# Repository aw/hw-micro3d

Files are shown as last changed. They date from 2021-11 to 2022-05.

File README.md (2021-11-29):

# μ3D

### RatRig V-Core 3 EVA wiring over RJ45

A toolboard that mounts on a 3D printer hotend assembly to enable wiring over RJ45.

PCB top view

| | | |
| :----: | :----: | :----: |
|  | OSHW_mark_JP000011 (https://certification.oshwa.org/jp000011.html) | Hackaday Logo (https://hackaday.io/project/180918-3d-ratrig-v-core-3-eva-wiring-over-rj45) |
| [Buy on Tindie](https://www.tindie.com/products/24538/) | [OSHW Certification](https://certification.oshwa.org/jp000011.html) | [Hackaday.io Project](https://hackaday.io/project/180918-3d-ratrig-v-core-3-eva-wiring-over-rj45) |

# Documentation

See the detailed documentation in the [docs/](docs/) directory:

  * [EXPLAIN](docs/EXPLAIN.md): learn the story behind this PCB, safety information, and OSHW
  * [HOWTO](docs/HOWTO.md): more detailed information on testing and wiring patterns
  * [REFERENCE](docs/REFERENCE.md): learn about the pinouts, trace widths, and other technical information
  * [TUTORIALS](docs/TUTORIALS.md): a quick guide to **get started** using this module

**Updated PCB v.2 now supports hotend heater cartridge, thermistor, and PWM fan.**

These instructions are for the **PCB v.2**. Please [click here to read instructions for PCB v.1](https://github.com/aw/hw-micro3d/releases/tag/v1).

**Note:** **PCB v.1 is not compatible with PCB v.2** due to the rerouted traces/wiring.

# Features

  * Form factor 80mm x 41mm
  * Lead-free, RoHS compliant
  * PCB traces are 0.5mm and can support at most 1A of current
  * High-current PCB traces are 3.0mm and can support at most 3.9A of current (2A tested)
  * Grounded M3 mounting holes connected to GND pins
  * Easy to source off-the-shelf through-hole components
  * Simple passive design draws 0mA current when no devices are connected

# Getting started

Click here to read the [tutorials](docs/TUTORIALS.md) quick guide to **get started**.

**DISCLAIMER: We are not responsible for accidents or problems caused by your use or misuse of these modules.**

# Notice

Usage of the logos and marks below are in no way an endorsement by their copyright and trademark owners.

* The Tindie and Hackaday logos are _Copyright © 2013, Supply Frame, Inc. All rights reserved._
* The OSHWA certification mark is _Trademark ™ 2018, the Open Source Hardware Association._

# License

μ3D: RatRig V-Core 3 EVA wiring over RJ45 and documentation © 2021 by [Alexander Williams](https://a1w.ca/) is licensed under [_CC BY-SA 4.0_ (Attribution-ShareAlike 4.0 International)](https://creativecommons.org/licenses/by-sa/4.0/).

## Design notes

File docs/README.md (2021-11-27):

# μ3D: Documentation

### RatRig V-Core 3 EVA wiring over RJ45

A toolboard that mounts on a 3D printer hotend assembly to enable wiring over RJ45.

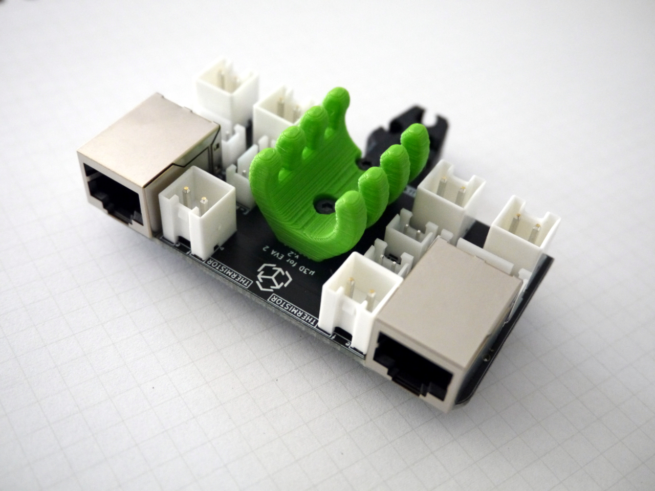
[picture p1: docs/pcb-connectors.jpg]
PCB with EVA mounts


**DISCLAIMER: We are not responsible for accidents or problems caused by your use or misuse of these modules.**

---

  * [EXPLAIN](EXPLAIN.md): learn the story behind this PCB, safety information, and OSHW
  * [HOWTO](HOWTO.md): more detailed information on testing and wiring patterns
  * [REFERENCE](REFERENCE.md): learn about the pinouts, trace widths, and other technical information
  * [TUTORIALS](TUTORIALS.md): a quick guide to **get started** using this module

# License

μ3D: RatRig V-Core 3 EVA wiring over RJ45 and documentation © 2021 by [Alexander Williams](https://a1w.ca/) is licensed under [_CC BY-SA 4.0_ (Attribution-ShareAlike 4.0 International)](https://creativecommons.org/licenses/by-sa/4.0/).

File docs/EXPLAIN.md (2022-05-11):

# μ3D: Explanation

### RatRig V-Core 3 EVA wiring over RJ45

A daughter board that mounts on a 3D printer hotend assembly to enable wiring over RJ45.

---

This document provides an explanation of the story behind this PCB module, safety information, and OSHW.

## Menu

  1. [Why another toolboard?](#1-why-another-toolboard)
  2. [Why did you make this?](#2-why-did-you-make-this)
  3. [Safety remarks](#3-safety-remarks)
  4. [Open Source Hardware](#4-open-source-hardware)

---

# 1. Why another toolboard?

There's a multitude of existing toolboards for 3D printers:

  * [Huvud 3D Tool Head](https://hackaday.io/project/174429-huvud-a-3d-printer-tool-head-controller-board)
  * [Voron Afterburner Tool-Head](https://www.onetwo3d.co.uk/product/voron-afterburner-tool-head-pcb/)
  * [Duet Toolboard](https://www.duet3d.com/Duet3Toolboard1LC)
  * [Carabiner PCB](https://github.com/Annex-Engineering/Annex_Engineering_PCBs/blob/master/carabiner-toolboard/buildguide/README.md)
  * [Pi G-Code Hat](https://oshwlab.com/matt_1626/pi-g-code-hat)

They are all great projects, but they are either much more complex, require many difficult to source components, or are simply unavailable / out of stock.

I wanted something designed specifically for the [EVA platform](https://main.eva-3d.page/) and which makes use of ubiquitous RJ45 cables.

# 2. Why did you make this?

Rather than wiring all devices directly from the 3D printer electronics panel to the hotend assembly, this module allows you to connect two simple RJ45 wires between them, and then wire the devices directly using the JST-XH / JST-VH connectors. One module mounts to the hotend, the other mounts on the electronics panel.

It then makes it simple to swap out a hotend without rewiring everything. It significantly cleans up the wiring and reduces maintenance and upgrading headache.

**Note:** This module was originally designed to lay flat with 40x40mm dimensions, but a similar project by _"Minty Trebor"_ on The RatRig Discord chat inspired me to alter the design.

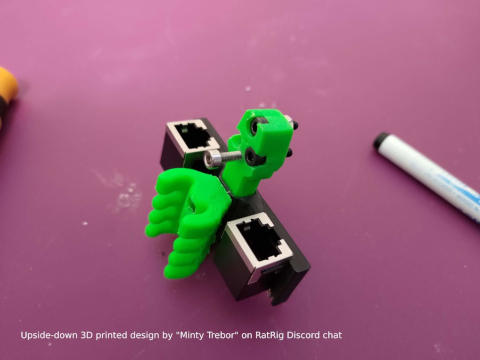
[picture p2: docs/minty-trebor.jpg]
Minty Trebor


# 3. Safety remarks

**Please use high-end stranded and shielded 24AWG RJ45 cables for safety and reliability.**

**Please use 16AWG stranded wiring for crimping to high current JST-VH connectors.**

Low current PCB traces are 0.5mm and can support at most 1A of current, although RJ45 wires of 26AWG size are rated for 350mA per wire, it is not recommended to pull too much current with such thin wires. The PCB does not contain any fuses or diodes to protect wiring or devices.

High current PCB traces are 3.00mm and can support at most 3.9A of current, and possibly more because the traces are doubled on both sides. **High current traces have only been tested up to 2A. Please be warned and use at your own risk.**

**Do not** connect a heater cartridge, or high power fan to the low-current JST-XH/RJ45 connectors. It is only designed for low-current devices and you will have a bad day if you decide to pull more than it can handle.

**Do not** connect anything other than a μ3D module to the RJ45 cables. It does not use any known standard pinouts and will likely destroy any "ethernet" devices you connect (laptops, switches, IP cameras, etc).

**Do** add your own fuses to protect your wiring and devices.

**DISCLAIMER: We are not responsible for accidents or problems caused by your use or misuse of these modules.**

# 4. Open Source Hardware

This project is [certified open hardware](https://certification.oshwa.org/jp000011.html) since August 23, 2021:

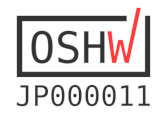
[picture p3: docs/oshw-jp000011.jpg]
OSHW_mark_JP000011 (https://certification.oshwa.org/jp000011.html)


If you have the time and patience for it, you're encouraged to generage the Gerbers from the KiCad EDA design files, and have them built by your local PCB fab. We built them through [JLCPCB](https://jlcpcb.com/) based in China.

Under the [CC BY-SA 4.0 License](https://creativecommons.org/licenses/by-sa/4.0/) if you make **changes** or **build upon** to the PCB design or documentation, please share them publicly so everyone may benefit from your improvements.

---

Now that you've read the explanation, feel free to browse the other documents below:

  * [HOWTO](HOWTO.md): more detailed information on testing and wiring patterns
  * [REFERENCE](REFERENCE.md): learn about the pinouts, trace widths, and other technical information
  * [TUTORIALS](TUTORIALS.md): a quick guide to **get started** using this module

# License

μ3D: RatRig V-Core 3 EVA wiring over RJ45 and documentation © 2021 by [Alexander Williams](https://a1w.ca/) is licensed under [_CC BY-SA 4.0_ (Attribution-ShareAlike 4.0 International)](https://creativecommons.org/licenses/by-sa/4.0/).

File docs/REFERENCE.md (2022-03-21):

# μ3D: Reference

### RatRig V-Core 3 EVA wiring over RJ45

A daughter board that mounts on a 3D printer hotend assembly to enable wiring over RJ45.

---

This document provides technical information about this module.

**DISCLAIMER: We are not responsible for accidents or problems caused by your use or misuse of these modules.**

## Menu

  1. [Technical specifications](#1-technical-specifications)
  2. [PCB pinout](#2-pcb-pinout)
  3. [Schematic](#3-schematic)
  4. [Bill of materials](#4-bill-of-materials)
  5. [Project logs](#5-project-logs)

---

# 1. Technical specifications

This PCB was designed with [KiCad EDA](https://kicad.org/) v5.1.9 from the `debian buster-backports` repository.

  * Form factor 80mm x 41mm
  * Lead-free, RoHS compliant
  * PCB traces are 0.5mm and can support at most 1A of current
  * High-current PCB traces are 3.0mm and can support at most 3.9A of current (2A tested)
  * High-current PCB traces are doubled on both sides of the PCB (for possibly ~7.8A current - not tested)
  * Grounded M3 mounting holes connected to GND pins
  * [Certified Open Source Hardware](https://certification.oshwa.org/jp000011.html) licensed under [CC BY-SA 4.0](https://creativecommons.org/licenses/by-sa/4.0/)

---

# 2. PCB pinout

Here's a render of the PCB from the front side:

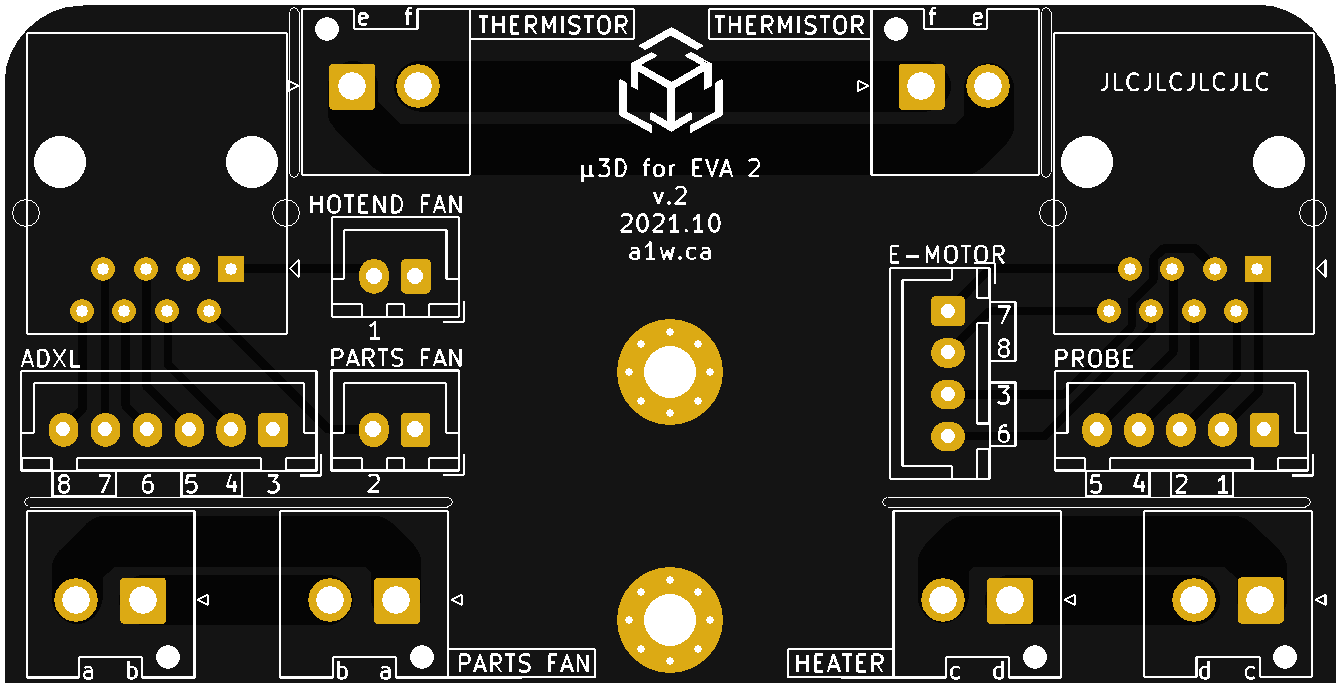
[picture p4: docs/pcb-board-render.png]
PCB board render


### Pin assigments

**Left side** as viewed from the front:

| Pin number / letter | Device | Type | Twisted pair |
| :----: | :---- | :---- | :---- |
| a | Parts fan | High-current | no |
| b | Parts fan | High-current | no |
| - | Parts fan (GND) | Low-current | no |
| 2 | Parts fan | Low-current | yes (pin 1) |
| | | |
| e | Thermistor | High-current | no |
| f | Thermistor | High-current | no |
| | | |
| - | Hotend fan (GND) | Low-current | no |
| 1 | Hotend fan | Low-current | yes (pin 2) |
| | | |
| 3 | ADXL (GND) | Low-current | yes (pin 6) |
| 4 | ADXL| Low-current | yes (pin 5) |
| 5 | ADXL | Low-current | yes (pin 4) |
| 6 | ADXL | Low-current | yes (pin 3) |
| 7 | ADXL | Low-current | yes (pin 8) |
| 8 | ADXL | Low-current | yes (pin 7) |

**Right side** as viewed from the front:

| Pin number / letter | Device | Type | Twisted pair |
| :----: | :---- | :---- | :---- |
| c | Heater | High-current | no |
| d | Heater | High-current | no |
| | | |
| e | Thermistor | High-current | no |
| f | Thermistor | High-current | no |
| | | |
| - | Probe (GND) | Low-current | no |
| 1 | Probe | Low-current | yes (pin 2) |
| 2 | Probe | Low-current | yes (pin 1) |
| 4 | Probe| Low-current | yes (pin 5) |
| 5 | Probe | Low-current | yes (pin 4) |
| | | |
| 3 | E-Motor | Low-current | yes (pin 6) |
| 6 | E-Motor | Low-current | yes (pin 3) |
| 7 | E-Motor | Low-current | yes (pin 8) |
| 8 | E-Motor | Low-current | yes (pin 7) |

> See the HOWTO docs for [Alternate wiring](HOWTO.md#4-alternate-wiring) alternate wiring of the endstop, thermistor, and parts fan.

---

# 3. Schematic

A PDF version of the schematic can be [downloaded here](../schematic-v2.pdf)

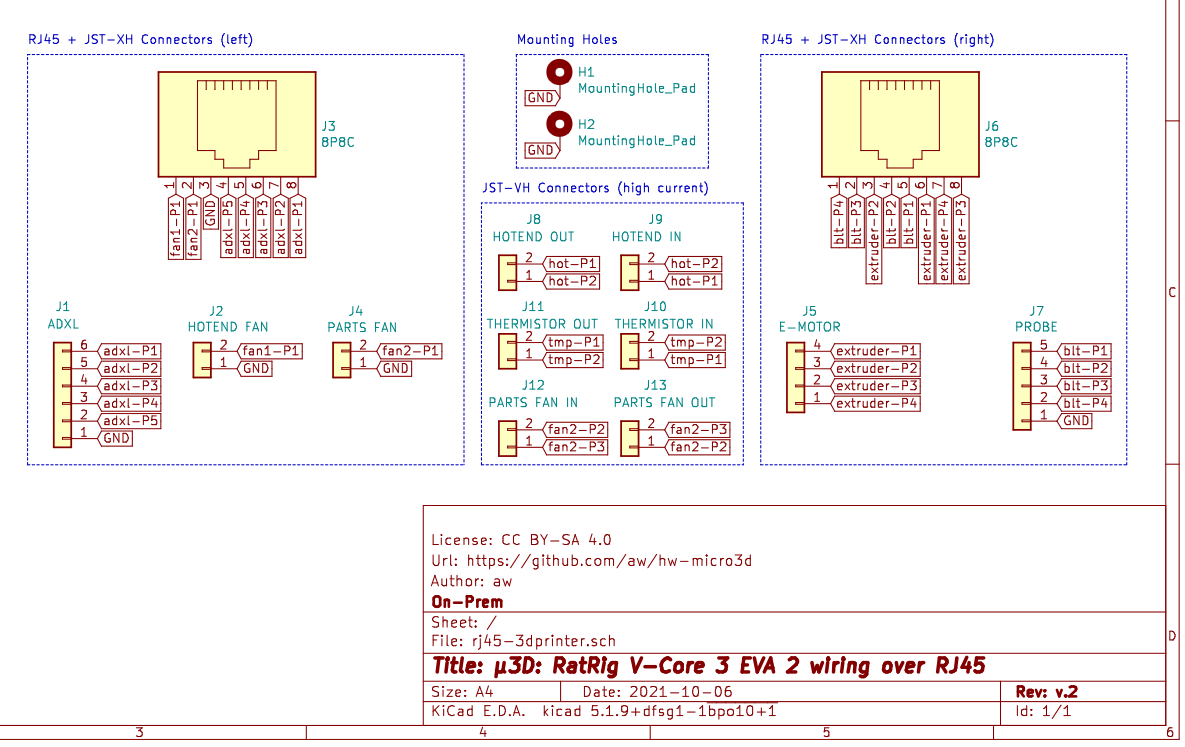
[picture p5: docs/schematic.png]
Schematic


---

# 4. Bill of materials

Below is the BOM list of through-hole components for one PCB:

| Quantity | Item and Description | Datasheet | Digikey Part # |
| :----: | :---- | :---- | :---- |
| 2 | RJ45/8P8C connector | [Assmann-RJ45-connector.pdf](../datasheets/Assmann-RJ45-connector.pdf) | A-2004-2-4-LP/FS-N-R |
| | | | |
| 2 | 2-pin JST-XH male and female connector (4 pcs) | [JST-XH connector.pdf](../datasheets/JST-XH-connector.pdf) | B2B-XH / XHP-2 |
| 1 | 4-pin JST-XH male and female connector (2 pcs) | | B4B-XH / XHP-4 |
| 1 | 5-pin JST-XH male and female connector (2 pcs) | | B5B-XH / XHP-5 |
| 1 | 6-pin JST-XH male and female connector (2 pcs) | | B6B-XH / XHP-6 |
| 19 | JST-XH socket for crimping | | SXH-001T-P0.6 |
| | | | |
| 6 | 2-pin JST-VH male and female connector (12 pcs) | [JST-VH connector.pdf](../datasheets/JST-VH-connector.pdf) | B2P-VH-FB-B |
| 12 | JST-VH socket for crimping | | |

---

# 5. Project logs

This project has been fully documented since its inception. It can be viewed on [Hackaday](https://hackaday.io/project/180918-3d-ratrig-v-core-3-eva-wiring-over-rj45). Care has been taken to document various design decisions and the technical details behind each iteration.

---

Now that you've read the technical reference, feel free to browse the other documents below:

  * [EXPLAIN](EXPLAIN.md): learn the story behind this PCB, safety information, and OSHW
  * [HOWTO](HOWTO.md): more detailed information on testing and wiring patterns
  * [TUTORIALS](TUTORIALS.md): a quick guide to **get started** using this module

# License

μ3D: RatRig V-Core 3 EVA wiring over RJ45 and documentation © 2021 by [Alexander Williams](https://a1w.ca/) is licensed under [_CC BY-SA 4.0_ (Attribution-ShareAlike 4.0 International)](https://creativecommons.org/licenses/by-sa/4.0/).

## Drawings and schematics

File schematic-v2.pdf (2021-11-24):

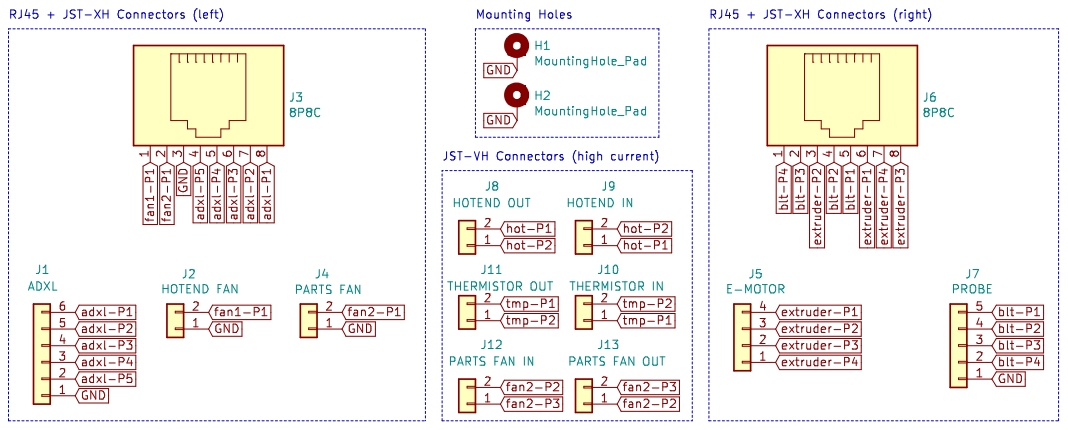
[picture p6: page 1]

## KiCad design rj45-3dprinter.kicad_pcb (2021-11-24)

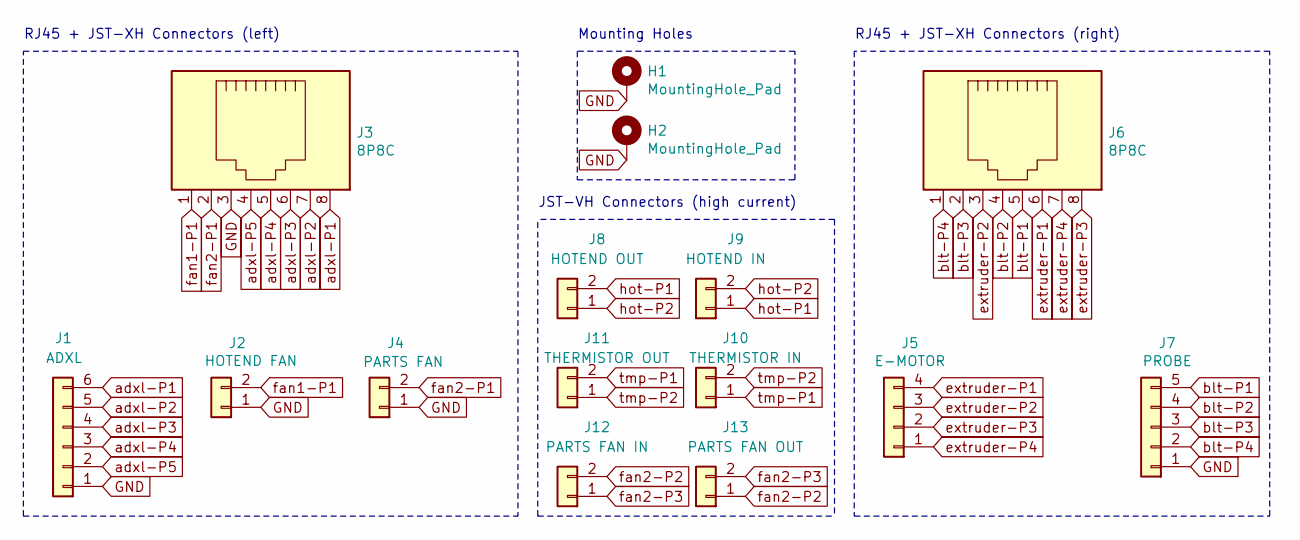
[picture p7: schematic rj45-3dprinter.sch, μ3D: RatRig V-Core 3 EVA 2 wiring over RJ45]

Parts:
H1, H2: MountingHole_Pad; MountingHole_3.2mm_M3_Pad_Via
J1: ADXL; JST_XH_B6B-XH-A_1x06_P2.50mm_Vertical
J2: HOTEND FAN; JST_XH_B2B-XH-A_1x02_P2.50mm_Vertical
J3, J6: 8P8C; RJ45_Amphenol_54602-x08_Horizontal_v02
J4: PARTS FAN; JST_XH_B2B-XH-A_1x02_P2.50mm_Vertical
J5: E-MOTOR; JST_XH_B4B-XH-A_1x04_P2.50mm_Vertical
J7: PROBE; JST_XH_B5B-XH-A_1x05_P2.50mm_Vertical
J8: HOTEND OUT; JST_VH_B2P-VH-FB-B_1x02_P3.96mm_Vertical
J9: HOTEND IN; JST_VH_B2P-VH-FB-B_1x02_P3.96mm_Vertical
J10: THERMISTOR IN; JST_VH_B2P-VH-FB-B_1x02_P3.96mm_Vertical
J11: THERMISTOR OUT; JST_VH_B2P-VH-FB-B_1x02_P3.96mm_Vertical
J12: PARTS FAN IN; JST_VH_B2P-VH-FB-B_1x02_P3.96mm_Vertical
J13: PARTS FAN OUT; JST_VH_B2P-VH-FB-B_1x02_P3.96mm_Vertical

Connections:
GND: H1.1, H2.1, J1.1, J2.1, J3.3, J4.1, J7.1
adxl-P1: J1.6, J3.8
adxl-P2: J1.5, J3.7
adxl-P3: J1.4, J3.6
adxl-P4: J1.3, J3.5
adxl-P5: J1.2, J3.4
blt-P1: J6.5, J7.5
blt-P2: J6.4, J7.4
blt-P3: J6.2, J7.3
blt-P4: J6.1, J7.2
extruder-P1: J5.4, J6.6
extruder-P2: J5.3, J6.3
extruder-P3: J5.2, J6.8
extruder-P4: J5.1, J6.7
fan1-P1: J2.2, J3.1
fan2-P1: J3.2, J4.2
fan2-P2: J12.2, J13.1
fan2-P3: J12.1, J13.2
hot-P1: J8.2, J9.1
hot-P2: J8.1, J9.2
tmp-P1: J10.1, J11.2
tmp-P2: J10.2, J11.1

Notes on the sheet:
Mounting Holes
RJ45 + JST-XH Connectors (left)
RJ45 + JST-XH Connectors (right)
JST-VH Connectors (high current)

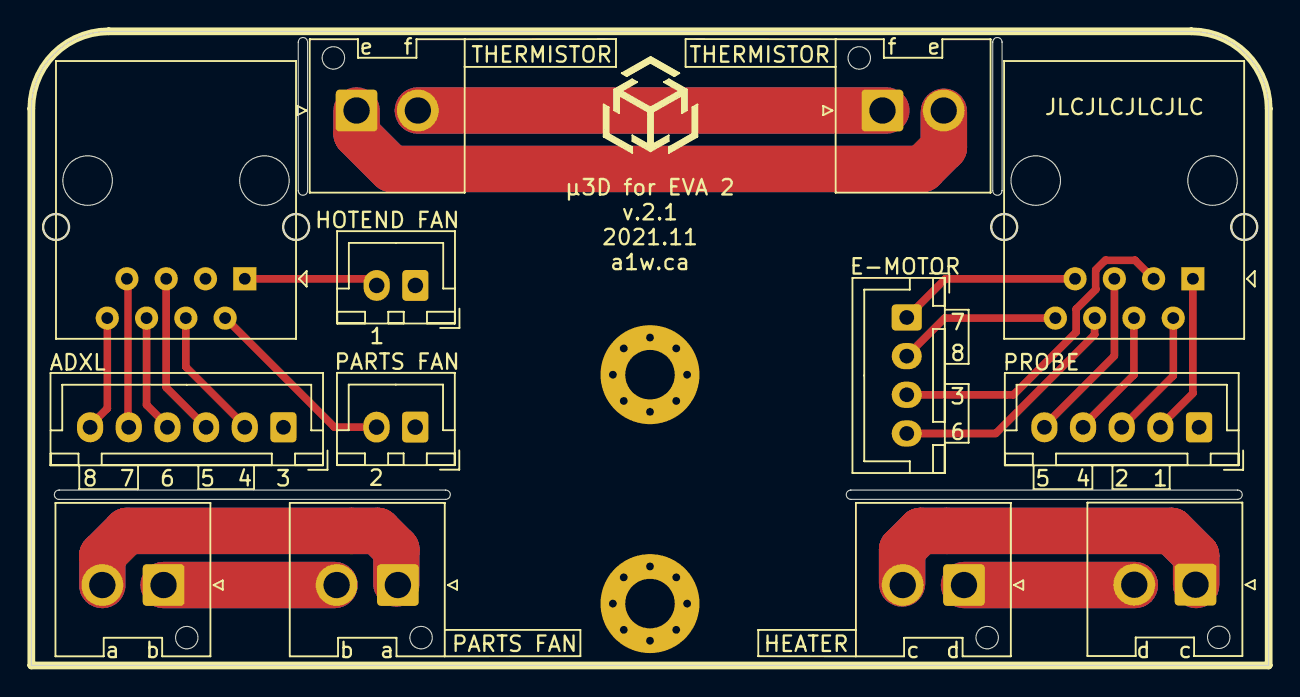
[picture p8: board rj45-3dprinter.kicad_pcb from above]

Board: 2 copper layers, 80.0 x 41.0 mm, 15 parts (0 on the bottom side), 22 nets.

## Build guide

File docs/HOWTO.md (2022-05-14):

# μ3D: Howto

### RatRig V-Core 3 EVA wiring over RJ45

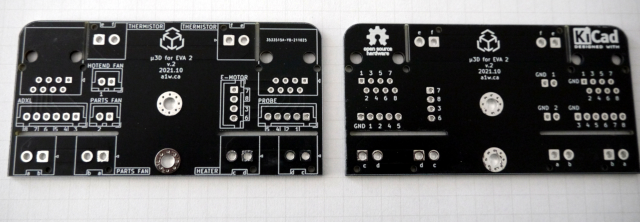
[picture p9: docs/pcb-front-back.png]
PCB front back


---

This document provides more detailed information on testing and wiring patterns.

**DISCLAIMER: We are not responsible for accidents or problems caused by your use or misuse of these modules.**

## Menu

  1. [Wiring a PWM fan](#1-wiring-a-pwm-fan)
  2. [Wiring a heater cartridge](#2-wiring-a-heater-cartridge)
  3. [Testing connections](#3-testing-connections)
  4. [Alternate wiring](#4-alternate-wiring)

PCB board render

# 1. Wiring a PWM fan

This PCB module is designed for 2 or 3-wire fans (ground, voltage, PWM signal).

**WARNING:** DO NOT try to control the fan speed of a 2-wire fan. It should/must be _always on_ (i.e: running 100% all the time).

Simple 2-wire fans only require a ground and voltage wire:

* If it's a low-current fan (less than 1A), it should be wired to the small JST-XH connector labeled "HOTEND FAN" (pins 1 and GND) or "PARTS FAN" (pins 2 and GND).

* If the fan is a high-current fan, the voltage and ground should be wired to the larger JST-VH connector labeled "PARTS FAN" (pins a and b).

A 3-wire fan with a PWM signal should have the PWM signal wired to the smaller JST-XH connector labeled "PARTS FAN" (pin 1), while the voltage and ground should be wired to the larger JST-VH connector labeled "PARTS FAN" (pins a and b).

# 2. Wiring a heater cartridge

The following wiring example is based on a _50W E3D V6_ which has a maximum current draw of 3.9A@12V, 2.8A@24V.

The high-current PCB traces (3.0mm) should theoretically support up to 3.9A of current with a 5deg C temperature rise (tested up to 2A), and the JST-VH connectors can support up to 10A.

Since the JST-VH connector labeled "HEATER" (pins c and d) is not electrically connected to anything else on the PCB, it should be safe to wire the heater cartridge directly to those pins. The heater cartridge wires do not have polarity, so they can be wired to `c` and `d` in any order.

# 3. Testing connections

After soldering all components to the PCB, a good way to ensure there were no mistakes is to perform an electrical continuity test using a multimeter.

One probe should touch a pin on the back of the RJ45 connector, and the other probe should touch the corresponding (numbered) pin on the JST-XH connector. For example: pin 1 on the left RJ45 should match pin 1 on the "HOTEND FAN". It should beep and/or light up to confirm the circuit is closed. Also make sure pin 1 doesn't match with pin 2 or other pins (if it does then you have a short / solder bridge).

For testing the JST-VH connectors, simply place a probe on corresponding (lettered) pins for each device. For example: pin e on the left "THERMISTOR" connector should match pin e on the right "THERMISTOR" connector. It should beep and/or light up to confirm the circuit is closed. Also make sure pin e doesn't match with pin f or other pins (if it does then you have a short / solder bridge).

One final thing to test is connectivity between two PCBs over the RJ45 cables. This should be done _before_ connecting actual devices.

As in the example above, pin 1 on the left RJ45 (on one PCB) should match pin 1 on the left RJ45 (on the other PCB). Do this for all 8 pins on both RJ45 connectors.

Perform a similar test with the wiring between both PCBs over the high-current wires (you're using 16AWG, right?).

---

  * [EXPLAIN](EXPLAIN.md): learn the story behind this PCB, safety information, and OSHW
  * [REFERENCE](REFERENCE.md): learn about the pinouts, trace widths, and other technical information
  * [TUTORIALS](TUTORIALS.md): a quick guide to **get started** using this module

# 4. Alternate wiring

In the situation where you also want to wire an endstop, thermistor, and have PWM control over the parts fans, all through the RJ45 cables, there is an alternate wiring scheme which can be used.

The idea is to use the ADXL pins **after tuning with the automatic [Input Shaper Calibration](https://www.klipper3d.org/Measuring_Resonances.html#input-shaper-auto-calibration)**. The ADXL does not need to be wired permanently, and it won't be used while the thermistor or fans are on (they'll cause too much noise), so it is possible to re-use those pins once calibration is complete.

Simply follow the wiring charts below.

### Alternate 1

**Left side** as viewed from the front:

| Pin number | Label | Device |
| :----: | :---- | :---- |
| a | PARTS FAN (high current) | unused |
| b | PARTS FAN (high current) | unused |
| e | THERMISTOR (high current) | unused |
| f | THERMISTOR (high current) | unused |
| 1 | HOTEND FAN | Hotend fan + |
| - | HOTEND FAN (GND) | Hotend fan - |
| 2 | PARTS FAN | Endstop + |
| - | PARTS FAN (GND) | Endstop - |
| 3 | ADXL (GND) | unused |
| 4 | ADXL | Thermistor |
| 5 | ADXL | Thermistor |
| 6 | ADXL | Endstop signal |
| 7 | ADXL | Parts fan + |
| 8 | ADXL | Parts fan - |

### Alternate 2

**Left side** as viewed from the front:

| Pin number | Label | Device |
| :----: | :---- | :---- |
| a | PARTS FAN (high current) | unused |
| b | PARTS FAN (high current) | unused |
| e | THERMISTOR (high current) | Thermistor |
| f | THERMISTOR (high current) | Thermistor |
| 1 | HOTEND FAN | unused |
| - | HOTEND FAN (GND) | unused |
| 2 | PARTS FAN | Endstop + |
| - | PARTS FAN (GND) | Endstop - |
| 3 | ADXL (GND) | unused |
| 4 | ADXL | Hotend fan + |
| 5 | ADXL | Hotend fan - |
| 6 | ADXL | Endstop signal |
| 7 | ADXL | Parts fan + |
| 8 | ADXL | Parts fan - |

# License

μ3D: RatRig V-Core 3 EVA wiring over RJ45 and documentation © 2021 by [Alexander Williams](https://a1w.ca/) is licensed under [_CC BY-SA 4.0_ (Attribution-ShareAlike 4.0 International)](https://creativecommons.org/licenses/by-sa/4.0/).

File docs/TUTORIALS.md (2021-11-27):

# μ3D: Tutorials

### RatRig V-Core 3 EVA wiring over RJ45

A daughter board that mounts on a 3D printer hotend assembly to enable wiring over RJ45.

---

This document provides a quick guide to **get started** using this module.

**DISCLAIMER: We are not responsible for accidents or problems caused by your use or misuse of these modules.**

## Menu

There are currently **five (5)** starter tutorials.

  1. [Order the PCB kit](#1-order-the-pcb-kit)
  2. [Solder the components](#2-solder-the-components)
  3. [Crimp the connectors](#3-crimp-the-connectors)
  4. [Connect the devices](#4-connect-the-devices)
  5. [Start printing](#5-start-printing)

This PCB and documentation was created by [aw](https://github.com/aw). If you find or have any bugs, issues, or feature requests, please [create an issue](https://github.com/aw/hw-micro3d/issues/new).

You can also join the discussion on channel `#eva-contrib` on the [RatRig Discord](https://discord.gg/n9MrbAq5).

---

# 1. Order the PCB kit

If you haven't purchased the PCB kit already, now's your chance:

[Buy from Tindie](https://www.tindie.com/products/24538/)

 

---

# 2. Solder the components

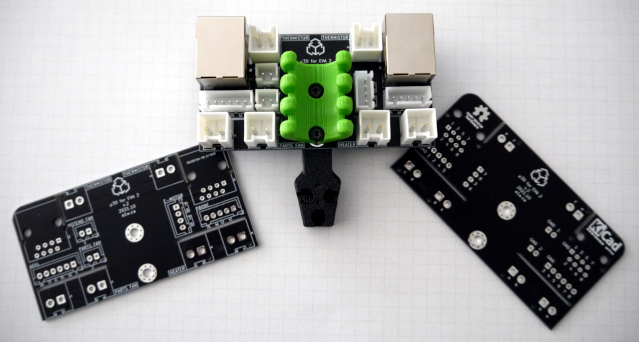
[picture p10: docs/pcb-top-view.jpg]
PCB top view


**Note:** Please use lead-free solder for all components.

**Note:** Before soldering, please ensure there is proper ventilation, and wear a mask or use a fume extractor if possible.

### Test-fit components

Before soldering, test-fit all the JST-XH and JST-VH connectors to confirm their final location and placement. This step is very difficult to get wrong.

### Solder time

1. Start with the smaller JST-XH connectors. Insert all the connectors and cover them with masking tape or
kapton tape so they don’t move, then flip the board and solder them carefully.
2. Solder the larger JST-VH connectors next. Again, cover them with tape so they don't move.
3. Finally, solder the RJ-45 connectors. Insert the RJ-45 connectors then bend the two side pins for stability.

### Verify your work

It's always a good idea to verify each solder connection's continuity with a multimeter, and ensure there are no bridges with nearby pins.

See the [Testing Connections howto](HOWTO.md#3-testing-connections) to learn more about testing the solder connections.

---

# 3. Crimp the connectors

Crimping connectors can be time consuming and error-prone. For the best results, it's recommended to have a **good** crimp tool such as an _Engineer PA-21_ and _Engineer PA-20_ for larger crimps.

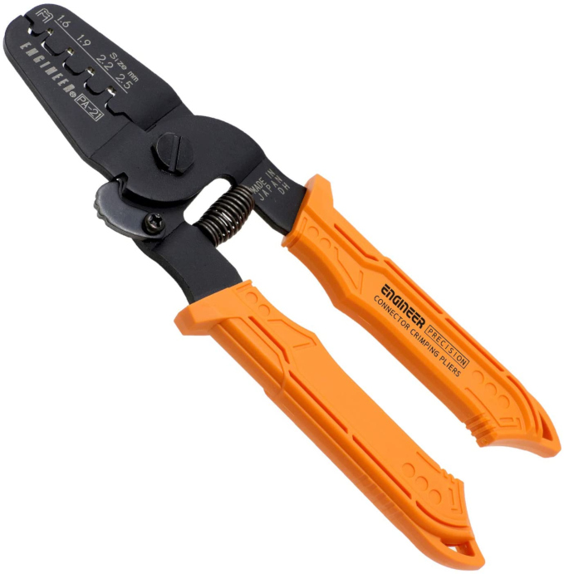
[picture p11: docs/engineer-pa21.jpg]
Engineer PA-21


Also ensure you have the correct size wires:

* JST-XH crimps support wires 30AWG to 22AWG.
* JST-VH crimps support wires 22AWG to 16AWG.

Lower gauge (ex: 16AWG) can support higher currents compared to higher gauge (ex: 22AWG).

**Note:** Make sure you don't shorten wires too much, leave some room for mistakes and future changes.

The PCB kit includes one extra crimp per PCB. That means you're free to make a mistake, but only one ;)

---

# 4. Connect the devices

### Wire the devices

Wiring devices, such as the thermistor, fans, probe, etc, can be irreversible. If a mistake was made during crimping or soldering, it **could destroy your devices**.

**Note:** Make sure the 3D printer **is off** before connecting devices for the first time.

### Wire the RJ45 cables

Connect the RJ45 cables between the two PCBs.

**Note:** Please use high-end stranded and shielded 24AWG RJ45 cables for safety and reliability.

### Mount the PCBs

Make sure to mount the PCBs to your electronics panel and hotend using the grounded M3 mounting holes.

Congratulations! If you've made it this far, then you're almost ready to start 3D printing.

---

# 5. Start printing

Turn on your 3D printer, and make some final verifications:

### Verify temperatures

Ensure the wires and cabling aren't getting hot. They should not feel hot after simply turning on the printer. If they do, you might have incorrect wiring and this **could be dangerous**.

### Verify voltages

Ensure the voltages to each device are correct (ex: 24V for the thermistor, 12V for the fan, etc).

### Make a test print

Make a test print, while checking the temperatures of all wiring during printing. Everything should feel _normal_. Smoke is a bad sign, fire is a really bad sign. It's a good idea to avoid those.

See the [Safety remarks explanation](EXPLAIN.md#3-safety-remarks) to read more safety recommendations.

---

Now that you've completed all the tutorials, you're ready to read the other documents below:

  * [EXPLAIN](EXPLAIN.md): learn the story behind this PCB, safety information, and OSHW
  * [HOWTO](HOWTO.md): more detailed information on testing and wiring patterns
  * [REFERENCE](REFERENCE.md): learn about the pinouts, trace widths, and other technical information

# License

μ3D: RatRig V-Core 3 EVA wiring over RJ45 and documentation © 2021 by [Alexander Williams](https://a1w.ca/) is licensed under [_CC BY-SA 4.0_ (Attribution-ShareAlike 4.0 International)](https://creativecommons.org/licenses/by-sa/4.0/).

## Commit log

2021-08-15 Add design files
    [rj45-3dprinter.kicad_pcb, rj45-3dprinter.sch]
2021-08-15 Add schematic and pinout
2021-08-15 Add image of bare PCBs
2021-11-24 Update PCB for hotend (high-current) components
    [rj45-3dprinter.kicad_pcb, rj45-3dprinter.sch]
2022-03-21 Add alternate wiring scheme to documentation
2022-05-11 Update documentation note about 2-wire fans and thermistor.
    Thanks to Mitsuma for the heads-up
2022-05-14 Add warning about speed control of a 2-wire fan

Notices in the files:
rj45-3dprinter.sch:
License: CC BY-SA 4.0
